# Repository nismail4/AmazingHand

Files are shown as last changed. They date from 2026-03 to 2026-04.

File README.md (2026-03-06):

Project is licensed under [Apache 2.0](https://www.apache.org/licenses/LICENSE-2.0)

Mechanical design is licensed under a:
[Creative Commons Attribution 4.0 International License][cc-by].
[][cc-by]
[][cc-by]

[cc-by]: http://creativecommons.org/licenses/by/4.0/
[cc-by-image]: https://licensebuttons.net/l/by/4.0/88x31.png
[cc-by-shield]: https://img.shields.io/badge/License-CC%20BY-lightgrey.svg

# Amazing Hand project

Patterns

Robotic hands are often very expensive and not so expressive. More dexterous ones often need cables and deported actuators in the forearm, i.e.,

The aim of this project is to be able to explore humanoid hand possibilities on a real robot (and Reachy2 is the perfect candidate for that !) with moderate cost.
=> Wrist interface is designed for Reachy2's wrist (Orbita 3D), but it can be easily adapted to other robot's wrist...

Reachy

Amazing Hand is:
- 8 dofs humanoid hand with 4 fingers
- 2 phalanxes per finger articulated together
- flexible shells almost everywhere
- All actuators inside the hand, without any cables
- 3D printable
- 400g weight
- low-cost (<200€)
- open-source

[AmazingHand_Overview](/docs/AmazingHand_Overview.pdf)

Hand Overview
Each finger is driven by a parallel mechanism. 
That means 2x small Feetech SCS0009 servos are used to move each finger in flexion/extension and abduction/adduction

Finger Overview

Two control methods are available:
- Use a serial bus driver (Waveshare i.e.) + Python script
- Use an Arduino + Feetech TTL Linker

Detailed explanations are available for both ways, and basic demo software is also available.
Up to you !

## Table of contents

- [Build Resources](#build-resources)
    - [BOM (Bill Of Materials)](#bom-bill-of-materials)
    - [CAD Files and Onshape document](#cad-files-and-onshape-document)
    - [Assembly Guide](#assembly-guide)
    - [Run_basic_Demo](#run-basic-demo)    
- [Disclaimer](#disclaimer)
- [AmazingHand advanced Demo](#amazinghand-advanced-demo)   
- [Don't want to build it by yourself? Kits are available!](#don't-want-to-build-it-by-yourself-?)    
- [Project Updates & Community](#project-updates-&-community)
    - [To Do List](#to-do-list)
    - [FAQ](#faq)
    - [Contact](#contact)
    - [Thank you](#thank-you)

# Build Resources
## BOM (Bill Of Materials)
List of all needed components is available here:  
[AmazingHand BOM](https://docs.google.com/spreadsheets/d/1QH2ePseqXjAhkWdS9oBYAcHPrxaxkSRCgM_kOK0m52E/edit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)  
BOM

And remember to add control choice cost (2 options detailed previously)

Details for custom 3D printed parts are here: 
[3Dprinted parts](https://docs.google.com/spreadsheets/d/1QH2ePseqXjAhkWdS9oBYAcHPrxaxkSRCgM_kOK0m52E/edit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)

3Dparts

Here is a guide explaining how to print all the needed custom parts:
[=> 3D Printing Guide](/docs/AmazingHand_3DprintingTips.pdf)
3DPrint_example 

## CAD Files and Onshape document
STL and Steps files can be found [here](https://github.com/pollen-robotics/AmazingHand/tree/main/cad) 

Note that fingers are the same if you want to build a left hand, but some parts are symmetrical. Specific right hand parts are preceded by an "R", and other left hand parts by an "L".

Heart

Everyone can access the Onshape document too:   
[Link Onshape](https://cad.onshape.com/documents/430ff184cf3dd9557aaff2be/w/e3658b7152c139971d22c688/e/bd399bf1860732c6c6a2ee45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)  

Note that predefined positions are available in the "named position" tooling, with corresponding servo angles

Onshape&Named_Pos  

## Assembly Guide

Assembly guide for the Amazing Hand in combination with standard components in the BOM is here:  
[=> Assembly Guide](/docs/AmazingHand_Assembly.pdf)  
Assembly_example  

You will need a simple program / script to calibrate each finger, available here:
- With Python & Waveshare serial bus driver: [here](https://github.com/pollen-robotics/AmazingHand/tree/main/PythonExample)
- With Arduino & TTLinker: [here](https://github.com/pollen-robotics/AmazingHand/tree/main/ArduinoExample)

Note that this assembly guide is for a standalone right hand.

If you need to build a standalone left hand, you can keep the same IDs for servo locations, and select if it's a right or left hand in the software.

## Run basic Demo

A basic demo is available with both Python & Arduino.

You will need an external power supply to be able to power the 8 actuators inside the hand.

If you don't have one already, a simple external power supply could be a DC/DC 220V -> 5V / 2A adapter with jack connector.
Check on the BOM list:
[AmazingHand BOM](https://docs.google.com/spreadsheets/d/1QH2ePseqXjAhkWdS9oBYAcHPrxaxkSRCgM_kOK0m52E/edit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) 

- Python script: "AmazingHand_Demo.py" [here](https://github.com/pollen-robotics/AmazingHand/tree/main/ArduinoExample)
  
- Arduino program: "AmazingHand_Demo.ino" [here](https://github.com/pollen-robotics/AmazingHand/tree/main/PythonExample)

https://github.com/user-attachments/assets/485fc1f4-cc57-4e59-90b5-e84518b9fed0

## You need both right & left hands on the same bus ?

If you need to build both right and left hands to plug them on a robot, you will have to attribute different IDs for right and left hands. You can't have same ID for different servos on the same serial bus...
Very important thing is to keep same assembly order for servos, but set them different IDs than for the right hand, as follows:
IDs

Specific software is also needed, in order to drive each hand independently.
This simple demo runs the same hand patterns on both hands simultaneously, but it's only available in Python:
"AmazingHand_Demo_Both" [here](https://github.com/pollen-robotics/AmazingHand/tree/main/PythonExample)

# Disclaimer

I noticed some variations between theoretical angles for Flexion / Extension, Abduction / Adduction and angles in real life prototypes. This is probably due to several sources of variation (3D printed parts are not perfect, balljoint rods are manually adjusted one by one, servo horn rework, flexibility of plastic parts...).

This design has not yet been tested for long and complex prehensile tasks. Before being able to grasp objects safely (that means without damaging servos or mechanical parts), a kind of smart software needs to be built.
SCS0009 servos have smart capabilities as:
- Torque enable / disable
- Torque feedback
- Current position sensor
- Heat temperature feedback
- ...

# AmazingHand advanced Demo
Tracking demo (https://www.youtube.com/watch?v=U0TfeG3ZUto)

For more advanced usage using inverse/forward kinematics there are several examples in the [Demo](Demo) directory along with some useful tools to test/configure the motors.

# Don't want to build it by yourself?
=> Kits are available here :

Seeed Studio :
https://www.seeedstudio.com/Amazing-Hand-Right-Hand-The-Open-Source-Robotic-Hand-Developer-Kit.html

WowRobo :
https://shop.wowrobo.com/products/amazing-hand-the-open-source-robotic-hand-kit

# Project Updates & Community
## Updates from community

- ### Amazing Base for the amazing hand : 
Base
STL or Step file can be found [here](https://github.com/pollen-robotics/AmazingHand/tree/main/cad) 

- ### Specific Chinese BOM available here :
[Chinese BOM](https://docs.google.com/spreadsheets/d/1fHZiTky79vyZwICj5UGP2c_RiuLLm89K8HrB3vpb2h4/edit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)

Thanks to Jianliang Shen !

- ### Amazing hand with SG90 servos + force control setup 🔥

Force_control
Force_control_setup

GitHub with code: (https://github.com/joanbox24/AmazingHand-with-sg90-servo-force-control)

- ### Amazing hand interface for SO-Arm 🔥

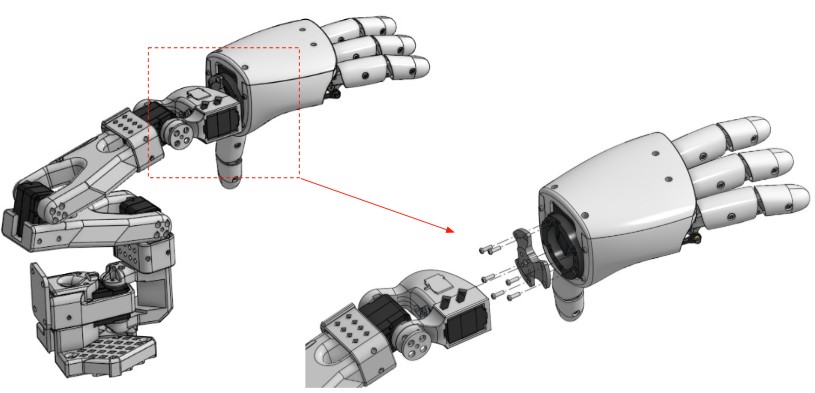
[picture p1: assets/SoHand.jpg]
SoHand


STL or Step file can be found [here](https://github.com/pollen-robotics/AmazingHand/tree/main/cad)
Or directly on onshape workspace, folder "community update"

## To Do List
- Design small custom pcb with serial hub and power supply functions, to fit everything in the hand
- Test with prehensile tasks 
      => Add smarter behaviour for closing hand, based on available motors feedbacks
- Study possibility to have 4 different fingers length, or add a 5th finger
- Study possibility to use STS3032 Feetech motors instead of SCS0009
      => Stronger for quite the same volume, but servo horn is different
- Study possibility to add compliancy by replacing rigid links to springs
- Add fingertip sensor to push one step higher smart control

## FAQ
WIP

## Contact

You can reach public discord channel here : 
[Discord AmazingHand](https://discord.com/channels/519098054377340948/1395021147346698300)

Or 
[Contact me or Pollen Robotics](/docs/contact.md)

## Thank you
Huge thanks to those who have contributed to this project so far:
- [Steve N'Guyen](https://github.com/SteveNguyen) for beta testing, Feetech motors integration in Rustypot, Mujoco/Mink and hand tracking demo
- [Pierre Rouanet](https://github.com/pierre-rouanet) for Feetech motors integration in pypot  
- [Augustin Crampette](https://fr.linkedin.com/in/augustin-crampette) & [Matthieu Lapeyre](https://www.linkedin.com/in/matthieulapeyre/) for open discussions and mechanical advices

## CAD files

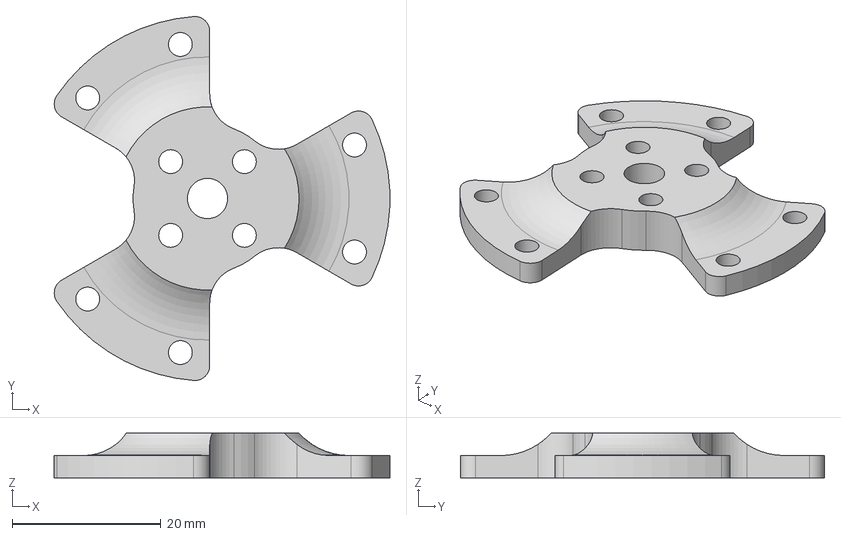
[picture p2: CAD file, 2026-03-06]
cad/step/SO-ARM_Interface.step
45.0 x 48.9 x 6.00 mm

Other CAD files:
cad/stl/SO-ARM_Interface.stl

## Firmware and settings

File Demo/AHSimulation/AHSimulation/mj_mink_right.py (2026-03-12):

"""Mujoco Client: This node is used to represent simulated robot, it can be used to read virtual positions, or can be controlled."""

import argparse

import os
import time

import mujoco
import mujoco.viewer
import pyarrow as pa
from dora import Node

import mink
from loop_rate_limiters import RateLimiter
from mink.contrib import TeleopMocap
from pathlib import Path
import numpy as np

ROOT_PATH = Path(os.path.dirname(os.path.abspath(__file__))).parent


class Client:
    """TODO: Add docstring."""

    def __init__(self, mode='pos'):
        """TODO: Add docstring."""


        self.model = mujoco.MjModel.from_xml_path(
            f"{ROOT_PATH}/AHSimulation/AH_Right/mjcf/scene.xml"
        )
        # self.data=mujoco.MjData(self.model)


        self.configuration = mink.Configuration(self.model)

        self.posture_task = mink.PostureTask(self.model, cost=1e-2)

        if mode=='pos':
            self.task1 = mink.FrameTask(
                frame_name='tip1',
                frame_type="site",
                position_cost=1.0,
                orientation_cost=0.0,
                lm_damping=1.0,
            )

            self.task2 = mink.FrameTask(
                frame_name='tip2',
                frame_type="site",
                position_cost=1.0,
                orientation_cost=0.0,
                lm_damping=1.0,
            )

            self.task3 = mink.FrameTask(
                frame_name='tip3',
                frame_type="site",
                position_cost=1.0,
                orientation_cost=0.0,
                lm_damping=1.0,
            )

            self.task4 = mink.FrameTask(
                frame_name='tip4',
                frame_type="site",
                position_cost=1.0,
                orientation_cost=0.0,
                lm_damping=1.0,
            )
        elif mode=='quat': #we control the orientation
            self.task1 = mink.FrameTask(
                frame_name='tip1',
                frame_type="site",
                position_cost=0.0,
                orientation_cost=1.0,
                lm_damping=1.0,
            )

            self.task2 = mink.FrameTask(
                frame_name='tip2',
                frame_type="site",
                position_cost=0.0,
                orientation_cost=1.0,
                lm_damping=1.0,
            )

            self.task3 = mink.FrameTask(
                frame_name='tip3',
                frame_type="site",
                position_cost=0.0,
                orientation_cost=1.0,
                lm_damping=1.0,
            )

            self.task4 = mink.FrameTask(
                frame_name='tip4',
                frame_type="site",
                position_cost=0.0,
                orientation_cost=1.0,
                lm_damping=1.0,
            )
        else:
            #print(f"Error, unknown mode: {mode}")
            return -1
        # Regulate all equality constraints with the same cost.
        eq_task = mink.EqualityConstraintTask(self.model, cost=1000.0)

        self.tasks = [
            eq_task,
            self.posture_task,
            self.task1,
            self.task2,
            self.task3,
            self.task4,
        ]



        self.model = self.configuration.model
        self.data = self.configuration.data
        self.solver = "quadprog"

        self.motor_pos=[]
        self.metadata=[]
        self.node = Node()

    def run(self):
        """TODO: Add docstring."""
        with mujoco.viewer.launch_passive(self.model, self.data) as viewer:

            rate = RateLimiter(frequency=1000.0)
            # dt = rate.dt
            # t = 0
            self.configuration.update_from_keyframe("zero")

            # Initialize mocap bodies at their respective sites.
            self.posture_task.set_target_from_configuration(self.configuration)

            mink.move_mocap_to_frame(self.model, self.data, "finger1_target", "tip1", "site")
            mink.move_mocap_to_frame(self.model, self.data, "finger2_target", "tip2", "site")
            mink.move_mocap_to_frame(self.model, self.data, "finger3_target", "tip3", "site")
            mink.move_mocap_to_frame(self.model, self.data, "finger4_target", "tip4", "site")


            for event in self.node:
                event_type = event["type"]

                if event_type == "INPUT":
                    event_id = event["id"]

                    if event_id == "tick":
                        # self.node.send_output("tick", pa.array([]), event["metadata"])

                        if not viewer.is_running():
                            break

                        step_start = time.time()



                        self.task1.set_target(
                            mink.SE3.from_mocap_name(self.model, self.data, "finger1_target")
                        )
                        self.task2.set_target(
                            mink.SE3.from_mocap_name(self.model, self.data, "finger2_target")
                        )
                        self.task3.set_target(
                            mink.SE3.from_mocap_name(self.model, self.data, "finger3_target")
                        )
                        self.task4.set_target(
                            mink.SE3.from_mocap_name(self.model, self.data, "finger4_target")
                        )





                        # vel = mink.solve_ik(self.configuration, self.tasks, self.model.opt.timestep, self.solver, 1e-5)
                        # self.configuration.integrate_inplace(vel, self.model.opt.timestep)
                        vel = mink.solve_ik(self.configuration, self.tasks, rate.dt, self.solver, 1e-5)
                        self.configuration.integrate_inplace(vel, rate.dt)



                        # Step the simulation forward
                        # mujoco.mj_step(self.m, self.data)

                        # mujoco.mj_step(self.model, self.data)


                        #get the motors position and send for real motor control

                        f1_motor1=mujoco.mj_name2id(self.model,mujoco.mjtObj.mjOBJ_JOINT,"finger1_motor1")
                        f1_motor2=mujoco.mj_name2id(self.model,mujoco.mjtObj.mjOBJ_JOINT,"finger1_motor2")
                        f2_motor1=mujoco.mj_name2id(self.model,mujoco.mjtObj.mjOBJ_JOINT,"finger2_motor1")
                        f2_motor2=mujoco.mj_name2id(self.model,mujoco.mjtObj.mjOBJ_JOINT,"finger2_motor2")
                        f3_motor1=mujoco.mj_name2id(self.model,mujoco.mjtObj.mjOBJ_JOINT,"finger3_motor1")
                        f3_motor2=mujoco.mj_name2id(self.model,mujoco.mjtObj.mjOBJ_JOINT,"finger3_motor2")
                        f4_motor1=mujoco.mj_name2id(self.model,mujoco.mjtObj.mjOBJ_JOINT,"finger4_motor1")
                        f4_motor2=mujoco.mj_name2id(self.model,mujoco.mjtObj.mjOBJ_JOINT,"finger4_motor2")
                        # #print(f"motor1: {self.data.joint(f1_motor1).qpos} motor2: {self.data.joint(f1_motor2).qpos}")
                        self.metadata=event["metadata"]
                        self.metadata["r_finger1"]=[0,1]
                        self.metadata["r_finger2"]=[2,3]
                        self.metadata["r_finger3"]=[4,5]
                        self.metadata["r_finger4"]=[6,7]

                        self.motor_pos=np.zeros(8);
                        self.motor_pos[self.metadata["r_finger1"]]=np.array([self.data.joint(f1_motor1).qpos[0],self.data.joint(f1_motor2).qpos[0]])
                        self.motor_pos[self.metadata["r_finger2"]]=np.array([self.data.joint(f2_motor1).qpos[0],self.data.joint(f2_motor2).qpos[0]])
                        self.motor_pos[self.metadata["r_finger3"]]=np.array([self.data.joint(f3_motor1).qpos[0],self.data.joint(f3_motor2).qpos[0]])
                        self.motor_pos[self.metadata["r_finger4"]]=np.array([self.data.joint(f4_motor1).qpos[0],self.data.joint(f4_motor2).qpos[0]])



                        viewer.sync()

                        # Rudimentary time keeping, will drift relative to wall clock.
                        time_until_next_step = self.model.opt.timestep - (
                            time.time() - step_start
                        )
                        if time_until_next_step > 0:
                            time.sleep(time_until_next_step)

                    elif event_id == "pull_position":
                        self.pull_position(self.node, event["metadata"])


                    elif event_id == "tick_ctrl":
                        if len(self.metadata)>0:
                            self.node.send_output("mj_r_joints_pos", pa.array(self.motor_pos), self.metadata)
                        # self.pull_position(self.node, event["metadata"])

                    elif event_id == "pull_velocity":
                        self.pull_velocity(self.node, event["metadata"])
                    elif event_id == "pull_current":
                        self.pull_current(self.node, event["metadata"])
                    elif event_id == "write_goal_position":
                        self.write_goal_position(event["value"])
                    elif event_id == "r_hand_pos":
                        self.write_mocap_pos(event["value"])
                    elif event_id == "r_hand_quat":
                        self.write_mocap_quat(event["value"])

                    elif event_id == "end":
                        break

                elif event_type == "ERROR":
                    raise ValueError(
                        "An error occurred in the dataflow: " + event["error"],
                    )

            self.node.send_output("end", pa.array([]))

    def pull_position(self, node, metadata):
        """TODO: Add docstring."""

    def pull_velocity(self, node, metadata):
        """TODO: Add docstring."""

    def pull_current(self, node, metadata):
        """TODO: Add docstring."""

    def write_goal_position(self, goal_position_with_joints):
        """TODO: Add docstring."""
        joints = goal_position_with_joints.field("joints")
        goal_position = goal_position_with_joints.field("values")

        for i, joint in enumerate(joints):
            self.data.joint(joint.as_py()).qpos[0] = goal_position[i].as_py()

    def write_mocap_pos(self, hand):

        #please, a method to access the mocap objects by name...

        if "r_tip1" in hand[0]:
            [x,y,z]=hand[0]['r_tip1'].values
            self.data.mocap_pos[0]=[x.as_py()*1.5-0.025,y.as_py()*1.5+0.022,z.as_py()*1.5+0.098]
        if "r_tip2" in hand[0]:
            [x,y,z]=hand[0]['r_tip2'].values
            self.data.mocap_pos[1]=[x.as_py()*1.5-0.025,y.as_py()*1.5-0.009,z.as_py()*1.5+0.092]
        if "r_tip3" in hand[0]:
            [x,y,z]=hand[0]['r_tip3'].values
            self.data.mocap_pos[2]=[x.as_py()*1.5-0.025,y.as_py()*1.5-0.040,z.as_py()*1.5+0.082]
        if "r_tip4" in hand[0]:
            [x,y,z]=hand[0]['r_tip4'].values
            self.data.mocap_pos[3]=[x.as_py()*1.5+0.024,y.as_py()*1.5+0.019,z.as_py()*1.5+0.017]


    def write_mocap_quat(self, hand):
        #please, a method to access the mocap objects by name...

        if "r_tip1" in hand[0]:
            [w,x,y,z]=hand[0]['r_tip1'].values
            self.data.mocap_quat[0]=[w.as_py(),x.as_py(),y.as_py(),z.as_py()]
        if "r_tip2" in hand[0]:
            [w,x,y,z]=hand[0]['r_tip2'].values
            self.data.mocap_quat[1]=[w.as_py(),x.as_py(),y.as_py(),z.as_py()]
        if "r_tip3" in hand[0]:
            [w,x,y,z]=hand[0]['r_tip3'].values
            self.data.mocap_quat[2]=[w.as_py(),x.as_py(),y.as_py(),z.as_py()]
        if "r_tip4" in hand[0]:
            [w,x,y,z]=hand[0]['r_tip4'].values
            self.data.mocap_quat[3]=[w.as_py(),x.as_py(),y.as_py(),z.as_py()]




def main():
    """Handle dynamic nodes, ask for the name of the node in the dataflow."""

    parser = argparse.ArgumentParser()
    parser.add_argument("-m", "--mode", type=str, choices=['pos','quat'], default='pos',
                    help="control mode: pos=position (we control the position of the tip) quat=quaternion (we control the orientation of the tip)")
    args = parser.parse_args()
    client = Client(args.mode)
    client.run()


if __name__ == "__main__":
    main()

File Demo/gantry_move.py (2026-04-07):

from dora import Node
import serial
import time

gantry = 0

def send_command(cmd):
    print(f"Sending: {cmd.strip()}")
    gantry.write(cmd.encode())

    timeout = time.time() + 2
    while time.time() < timeout:
        if gantry.in_waiting:
            response = gantry.readline().decode().strip()
            print(f"Arduino said: {response}")
            if "ok" in response or "ALARM" in response:
                return response
    return "TIMEOUT"
# 1. Initialize Gantry (USB-A port)
# Verify the COM port in Device Manager; it will be different from the hand (COM8)
gantry = serial.Serial('COM5', 115200, timeout=1) 
#time.sleep(2)
#send_command("$X\n")     # Unlock the startup alarm
#send_command("$H\n")
#time.sleep(90)
#send_command("G10 P0 L20 X0\n")
#send_command("G10 P0 L20 Y0\n")
#send_command("G90\n")    # Set to Absolute Mode (for tracking)
#send_command("G21\n")    # Ensure we are in Millimeters

# 1. Initialize and Home
send_command("$X\n") # Unlock startup alarm
print("Starting Homing Cycle...")
gantry.write(b"$H\n") # Start homing

# Instead of time.sleep(90), wait for the physical 'ok' from the homing finish
homing_complete = False
while not homing_complete:
    if gantry.in_waiting:
        line = gantry.readline().decode().strip()
        print(f"Homing status: {line}")
        if "ok" in line:
            homing_complete = True
    time.sleep(0.1)

# Post-Homing Setup
send_command("G90\n") # Absolute Mode
send_command("G21\n") # Millimeters

# --- Main Dora Loop ---
node = Node()
history_x, history_y = [], []
BUFFER_SIZE = 5
MOVE_THRESHOLD = 4.0  # mm (Adjust this: higher = steadier, lower = more sensitive)
SEND_INTERVAL = 0.04   # seconds (20Hz)
FEEDRATE = 8000        # mm/min adjust for gantry speed
SYNC_EVERY = 10
commands_sent = 0
last_target_x = 0
last_target_y = 0
last_send_time = 0

def send_init(cmd):
      gantry.write(cmd.encode())
      time.sleep(0.1)

send_init("G90\n") 
send_init("$110=5000\n") # Max speed X
send_init("$111=5000\n") # Max speed Y
send_init("$120=400\n")  # Acceleration X (High = Snappy)
send_init("$121=400\n")  # Acceleration Y (High = Snappy)

commands_sent = 0 
last_target_x = 0
last_target_y = 0
last_send_time = 0

print("Gantry ready. Starting loop...")

# --- Main Dora Loop ---
for event in node:
    if event["type"] == "INPUT" and event["id"] == "wrist_pos":
        try:
            # 1. Get Hand Pos
            val = event["value"].to_pylist()
            wrist = val[0] if isinstance(val[0], list) else val
            
            # 2. Map (330mm workspace)
            tx = (1 - max(0.1, min(0.9, wrist[0]))) * 330
            ty = (1 - max(0.1, min(0.9, wrist[1]))) * 330

            # 3. Micro-Smoothing
            history_x.append(tx); history_y.append(ty)
            if len(history_x) > BUFFER_SIZE:
                history_x.pop(0); history_y.pop(0)

            sx = sum(history_x) / len(history_x)
            sy = sum(history_y) / len(history_y)

            # 4. The Jogging Logic
            now = time.time()
            if now - last_send_time > SEND_INTERVAL:
                dx = abs(sx - last_target_x)
                dy = abs(sy - last_target_y)

                if dx > MOVE_THRESHOLD or dy > MOVE_THRESHOLD:
                    # THE SECRET SAUCE: 
                    # $J= (Jogging) is better than G0/G1 for real-time.
                    # It tells GRBL: "Go here now, and if a new $J comes, move there instead."
                    jog_cmd = f"$J=G21G90X{sx:.2f}Y{sy:.2f}F{FEEDRATE}\n"
                    gantry.write(jog_cmd.encode())
                    
                    last_target_x, last_target_y = sx, sy
                
                last_send_time = now

            # 5. Continuous Buffer Flush
            # If we don't read the 'ok' responses, the Arduino's output buffer fills up
            # and slows down the whole chip.
            if gantry.in_waiting:
                gantry.read_all()

        except Exception:
            continue

# for event in node:
#     if event["type"] == "INPUT" and event["id"] == "wrist_pos":
#         # Ensure we are converting the Arrow tensor/list correctly
#         try:
#             wrist_values = event["value"].to_pylist()
#             # If the output is a nested list like [[x, y]], take the first element
#             wrist = wrist_values[0] if isinstance(wrist_values[0], list) else wrist_values
            
#             wristx = wrist[0]
#             wristy = wrist[1]
#             print(f"Received Wrist: X={wristx:.2f}, Y={wristy:.2f}") # Debugging line
#         except Exception as e:
#             print(f"Data conversion error: {e}")
#             continue
#         # wrist[0] = X, wrist[1] = Y
#         wrist_values = event["value"].to_pylist()
#         wrist = wrist_values[0] if isinstance(wrist_values[0], list) else wrist_values
#         print(wrist)

#         wristx = wrist[0]
#         wristy = wrist[1]

#         if(wristx < 0.1):
#             wristx = 0.1

#         if (wristx > 0.9):
#             wristx = 0.9
        
#         if(wristy < 0.1):
#             wristy = 0.1

#         if (wristy > 0.9):
#             wristy = 0.9
        
#         # 2. Mapping to Workspace (Change 200 to your physical limit in mm)
#         target_x = (1 - wristx) * 330 #Flip X for gantry
#         target_y = (1 - wristy) * 330 # Flip Y for correct camera orientation
#         print(target_x,target_y)

#         history_x.append(target_x)
#         history_y.append(target_y)
#         if len(history_x) > BUFFER_SIZE:
#                 history_x.pop(0)
#                 history_y.pop(0)

#         smoothed_x = sum(history_x) / len(history_x)
#         smoothed_y = sum(history_y) / len(history_y)

#         current_time = time.time()
#         if current_time - last_send_time > SEND_INTERVAL:
            
#             # Calculate the delta (change) from the last move we actually sent
#             dx = abs(smoothed_x - last_target_x)
#             dy = abs(smoothed_y - last_target_y)

#             if dx > MOVE_THRESHOLD or dy > MOVE_THRESHOLD:
#                     # Construct and send the move
#                     command = f"G0 X{smoothed_x:.2f} Y{smoothed_y:.2f}\n"
#                     send_command(command)
                    
#                     # IMPORTANT: Update these so we have a new baseline for the next move
#                     last_target_x = smoothed_x
#                     last_target_y = smoothed_y
#                     last_send_time = current_time
#             else:
#                     # Optional: print for debugging to see if threshold is working
#                     # print(f"Ignored small move: dx={dx:.1f}, dy={dy:.1f}")
#                     pass

#             #command = f"G0 X{target_x:.2f} Y{target_y:.2f}\n"
#             # gantry.write(command.encode())
            
#             # Update the timestamp
#             # last_send_time = current_time
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

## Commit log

2026-01-29 Save current work
2026-01-30 Calibration, pinch and offset
2026-01-30 Add filter
2026-03-07 new gantry code

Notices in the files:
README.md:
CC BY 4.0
